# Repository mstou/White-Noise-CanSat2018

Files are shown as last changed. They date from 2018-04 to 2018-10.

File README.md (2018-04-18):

# White Noise
[White Noise](https://www.facebook.com/WhiteNoiseGRE/) is a space-engineering team from the National Technical University of Athens and currently consists of 6 members ( in alphabetical order ) :

 - Dimitris Bralios
 - Chariton Charitonidis
 - Iasonas Nikolaou
 - Spyros Pavlatos
 - George Rapakoulias
 - Miltiadis Stouras

Our team won 1st prize in the [CanSat in Greece 2018](https://cansat.gr/) competition.

# DrillSat
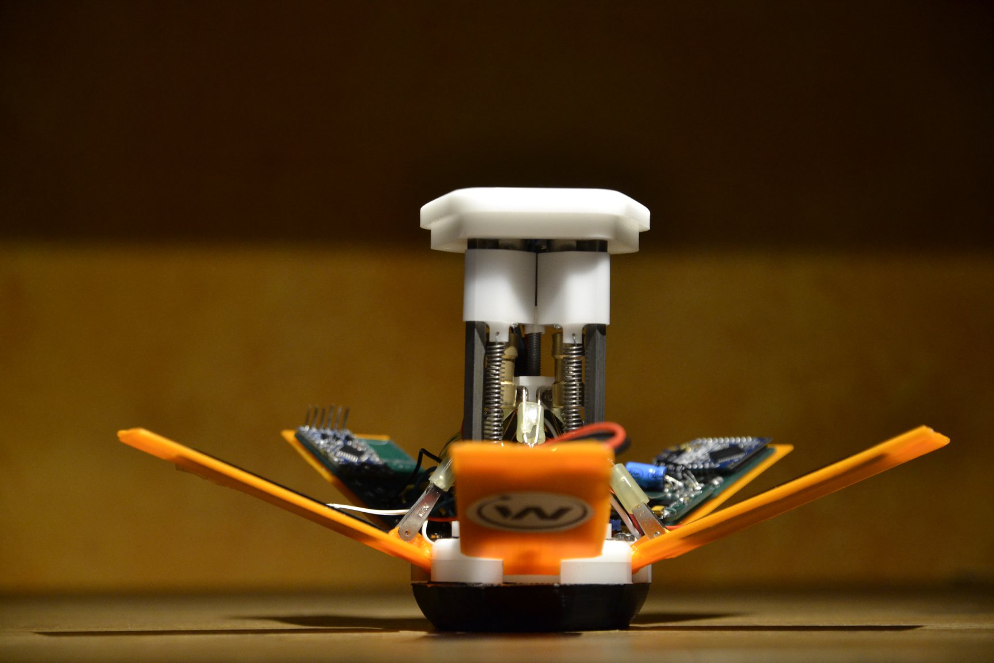
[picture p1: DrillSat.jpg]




This repository hosts the electrical circuits, mechanical drawings and software of our CanSat. Our goal was to develop a CanSat that can help in exploring new planets, as a part of our idea to use CubeSats in space exploration. Specifically, our CanSat, after a successful landing with the parachute, is able to use its [leg mechanism](https://www.youtube.com/watch?v=kTSUgSXn8OM) and rise into a position from which it can dig its drills to the ground and measure the soil's moisture with a sensor we developed.
You can find our ground station [here](https://github.com/MStou/CanSat2018-Ground-Station).

Our team, after facing many difficulties developing the prototype, decided to be fully open source and released all of our work to make sure that future teams will not have to "re-invent the wheel".

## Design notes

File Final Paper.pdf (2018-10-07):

## CFP-18-White-Noise

## CANSAT FINAL PAPER - DRILLSAT

### Authors Dimitris Bralios, bnbzor@gmail.com Chariton Charitonidis, haritoncharitonides@gmail.com Iasonas Nikolaou, iasonasnikolaou11@hotmail.com Spyros Pavlatos, spyrospavlatos4@gmail.com George Rapakoulias, george.rpk@outlook.com Miltiadis Stouras, m.stouras@gmail.com

Abstract: The CanSat in Greece competition aims at giving university students the opportunity to work on a multidisciplinary project with technology similar to that used in small satellites and to take their first steps in space. Moreover, the current trend in satellite technology which is to achieve more with a smaller probe, with prime examples being the CubeSats, makes this kind of competition more relevant. Our goal as a team was to design and build a CanSat that could be the basis for an actual space probe with the aim of extraterrestrial exploration. This paper presents our design of the CanSat discussing the mechanical, electrical and software aspects in detail, while showing that all the mission requirements are met. Specifically, our CanSat is launched onboard a research rocket and deployed at the apogee. Then a parachute is used to reach the nominal descent velocity. Equipped with five legs it is able to reach an upright position from where the drills can be activated. First, the leg and drill mechanisms are described in detail. Next, the selected sensors, the measurements taken and the electronics subsystem are discussed. Then, we present the flight software as well as the ground station that receives and visualizes the mission data in real time. Finally, we discuss the challenges we faced and draw conclusions.

CFP-18-White-Noise | Page 1 of 8

I. INTRODUCTION
The mission of our team for the 2018 CanSat in Greece competition consisted of the primary mission, same for all contestants, and the secondary one, selected by our team. In the primary mission we had to integrate sensors in our design, capable of measuring position, temperature and altitude during descent. The secondary mission was inspired from a number of real life projects in extraterrestrial exploration like the curiosity rover, the rosetta space probe, asteroid mining concepts etc. All those projects revolve around analysing the surface and soil of
planets | or | comets, | encountering | harsh
conditions. Our goal was to build a sensor for estimating soil moisture concentration and monitor it over time, in a supposed target planet, in order to further evaluate whether it could eventually host plants and support human activity. For further analysis, we added a UV sensor, since this is proven to be a key factor in the germination process.

II. PROJECT DESCRIPTION
The CanSat is launched onboard a Patriot type-rocket, with an apogee of 1 km where the probe is deployed. During the flight, a velocity of 500 km/h and an acceleration of 22 g could be reached. Next, throughout the descent the probe measures the barometric pressure, temperature and geographic coordinates. These measurements are stored as well as sent to the ground station in real time.
Requirements include the size of the probe, which has to fit inside a cylinder with a diameter of 65mm and a height of 115 mm. The descent rate after the deployment of the parachute should be in the range of 6 - 10 m/s. Also, the probe should be able to operate 4 hours continuously. Lastly, the mass of the CanSat should not exceed 350 grams.
Goal of the secondary mission is to measure the UV radiation and the soil moisture of the environment the CanSat is deployed in, from which we can exclude crucial information that can help us in our efforts to inhabit the target planet . After a successful landing with the parachute, it is able to use its leg mechanism and rise into a position from which it can dig its drills to the ground and measure the conductivity between the two drills, which is related to the moisture of the soil examined. Apart from the pressure and temperature sensor, a UV light sensor is added to determine if there is spectral content in the UV-A and UV-B range.
The data gathered are sent to the ground station, which is equipped with a high gain Yagi antenna with a range of 3 - 4 km. The frequency of the transmissions is 1 Hz. Through a web application the data received can be displayed and plotted in real time on a computer of the ground station.

III. MECHANICAL SYSTEM
In order to achieve our goals, a number of mechanisms had to be implemented in the design. The small size of the CanSat made it challenging to fit everything inside it in a robust way. After many prototypes, the following layout was chosen.

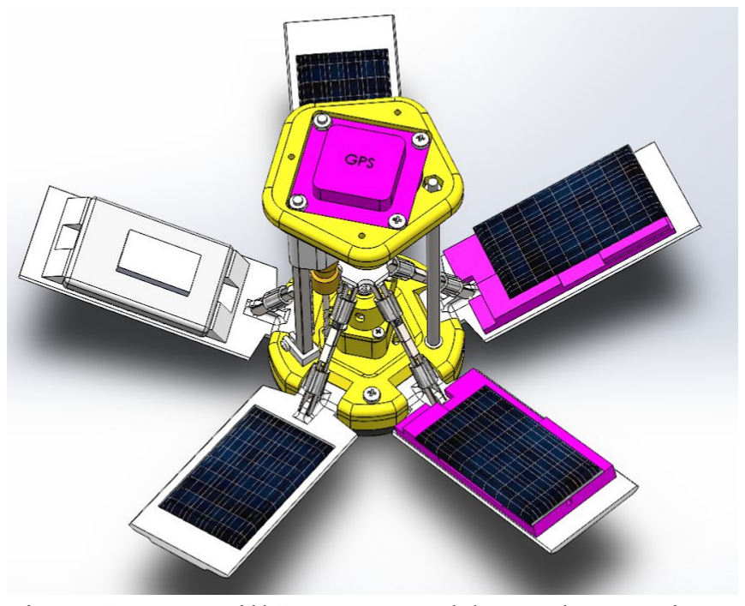
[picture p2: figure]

Fig. 1: DrillSat assembly, electronics represented with purple.

| All the electronics, the battery and the
solar panels were placed on the inside surface of the legs leaving space in the core of the CanSat for the drills and the leg deployment mechanism. A set of 5 foldable legs were placed in the periphery of the satellite, a number chosen to provide a good balance between leg width and near circular top view. A motor driven platform moving on a threaded rod, along with N clevis joints were used for deploying those legs. The length of each arm and the position of the joints were chosen carefully in order to give the mechanism an appropriate mechanical gain, allowing it to operate with a small motor and minimum current.

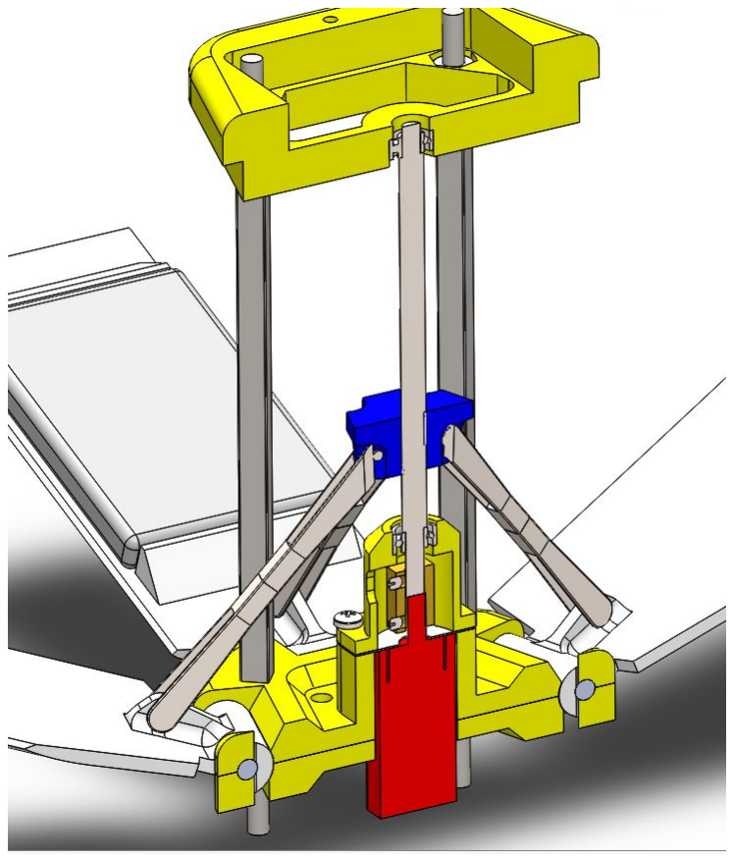
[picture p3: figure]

Fig. 2: Legs deployment mechanism

As for the drill mechanism, the drill assembly was sliding on a square 4x4 mm rod. In order to save space and weight, the assembly was moving with the aid of springs instead of actuators. An expendable retainer was used to prevent the drill from deploying. When voltage was applied to the motors, the drills would penetrate the retainer and protrude out of the CanSat, into the ground.

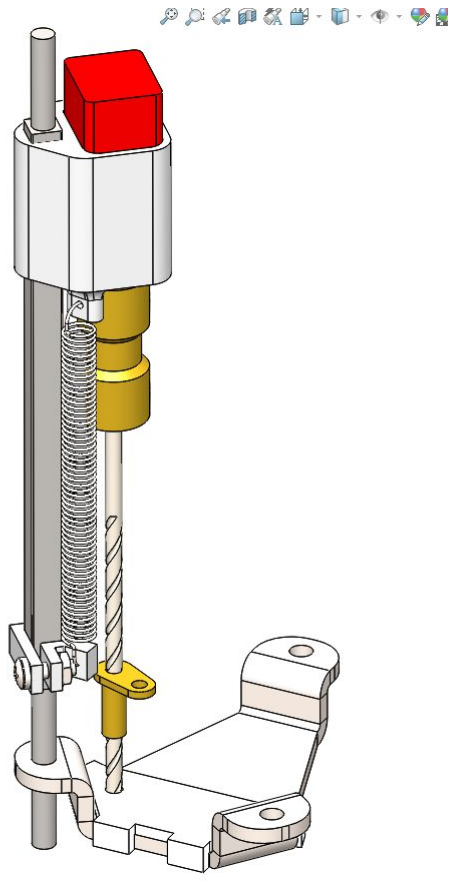
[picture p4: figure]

Fig. 3: Drill mechanism

Finally, in order to provide dampening in hard landings, some extra parts were added. A bottom made from TPC rubber was designed to make the first contact with the ground, absorbing most of the energy from the impact. Because the motor moving the legs was also located in the bottom of the satellite, we added a stainless steel metal cover around it.

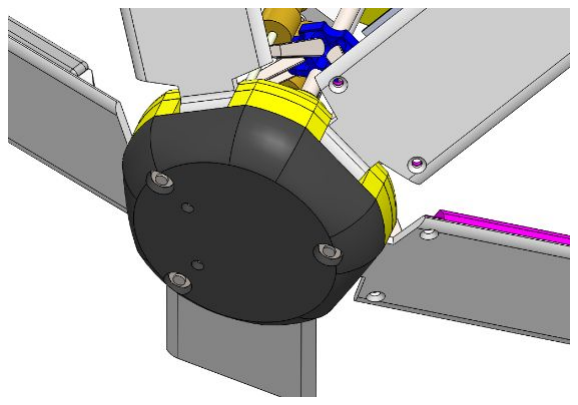
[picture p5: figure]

Fig. 4: Rubber damper

Most parts were CNC machined from POM plastic, ensuring high strength and dimensional precision. Metal parts were all made from stainless steel, with the exception of couplers, which were made from brass.
Apart from the satellite, we also constructed the parachute. We chose a classic circular design with a vent in the apex for stability. Its surface was first calculated theoretically using the following formula
F D = | [1]
2

CD

ρ V A

2

solved for A, given the terminal velocity (V), the total drag force (FD
), the air density (ρ) and the drag coefficient (CD

). After building the first prototype, fine-tuning was made in the surface area in order to achieve our target terminal velocity at 8 m/s, which we measured using image analysis from a video. Later on, for better precision, we also calculated the terminal velocity by conducting several drop tests in which we measured the height of the satellite in small constant time intervals and analyzed the measurements. The material we used was ripstop nylon. The diameter of the parachute was 48 cm and the diameter of the stability vent was 8 cm. A total of 8 buttonholes were made around the perimeter of the parachute fabric. A simple 2 mm kevlar thread was used for the suspension lines whose length was 50 cm enough to minimize the pitch of the CanSat.

IV. ELECTRONICS SYSTEM
The electronics system of the CanSat is comprised of an Arduino microcontroller, a UV sensor, a pressure and temperature sensor, a GPS, an XBee RF module anda conductivity sensor, all powered by a LiPo battery and four solar panels. The system apart from the battery the solar panels and the GPS, has to fit on top of two legs of the CanSat inside a space of 7x35x71 mm. Due to that two PCBs were designed so that the electronics can be mounted onto them. Also the structure had to be robust and survive any stresses, as well as being to run continuously for 4 hours, constricting the power budget.

IV.I. Sensor Subsystem
The UV light sensor used is ML8511 mounted on a board. Equipped with an internal amplifier it converts the photodiode current to voltage, outputting voltage linearly related to the UV light intensity measured in mW/cm

2
. The
sensor output is stable across the operating temperature range, from -25° C up to 75° C, although, when measuring in temperatures away from the one on which the sensor was calibrated, a slight error is introduced. The spectral response is highest in the range 280 - 390 nm which covers the UV-B spectrum and significant percentage of the UV-A spectrum. The typical supply current is around 300 μA at the operational voltage of 3 V.

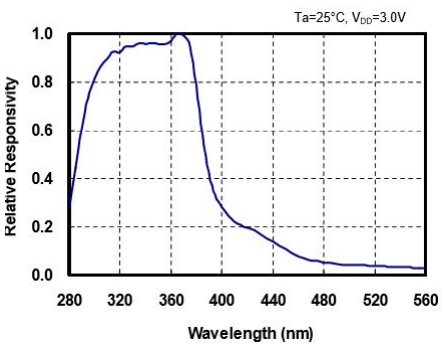
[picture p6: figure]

Fig. 5: Spectral response characteristics of ML8511

| The sensor used to measure temperature
and barometric pressure is BMP280. The interface used to communicate with the microcontroller is I2C. The pressure and temperature data, using the barometric formula, can give the current height with an accuracy of 1m. The operating pressure range is up to 9000 m above sea level and from -40° C to 85° C regarding the temperature range, while the typical current drawn is 2.7 μA.
The sensor used to measure the soil moisture is implemented as a voltage divider. Two high speed steel drills spaced 18.2mm apart are used to penetrate 20 mm in depth. One drill is connected to the ground voltage level through a 10K Ohm resistor while the other one to the +3.3 V level. The former drill is connected to an analog pin of the microcontroller. Given the voltage at that pin we can specify the resistance between them and then calculate the soil moisture.
The GPS module used is the LEA-6H, which is mounted on the top of the CanSat. It
sends | NAV-POSLLH | packages | to | the
microcontroller via serial connection, at a frequency of 1Hz. Typical supply current is 41 mA and 47 mA during the acquisition phase and the horizontal accuracy is 2.5 m.

IV.II. Communication and Data Handling The selected microcontroller board is the Arduino Pro Mini, using the ATmega328P, an 8-bit AVR microprocessor. It runs at 3.3 V and 8 MHz and has 14 input/output pins, 6 of them analog. The available program memory size is 32 KByte, as well as 1024 Bytes of non volatile EEPROM memory, used to make the CanSat state-aware after possible power offs. Apart from collecting and processing the measurements of the sensors the Arduino also controls the three motors through N-channel MOSFETS.
The RF module used for communication with the ground station is the XBee Pro S5 operating at 868MHz. It runs on 3.3 V consuming 60 mA at stand-by mode, 200 mA on packet emission and has a sensitivity of -112 dBm. It is used with an external antenna with 3 dBi gain which has the following radiation pattern.

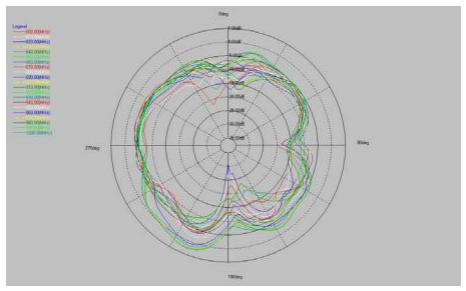
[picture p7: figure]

Fig. 6: Radiation pattern of the probe’s antenna

The same XBee module is also used on the ground station. The two modules are programmed to operate on AT Mode with ground station’s XBee being the coordinator and cansat’s XBee a router. Both modules transmit at a power of 25mW which is the legal local limit at 868MHz.

IV.III. Electrical Power Subsystem
A Polymer Lithium Ion battery, charged by four solar panels, is powering the CanSat. The battery has a voltage output of 3.7 V and a capacity of 980 mAh. Four 30.5 mm by 58.5 mm solar panels connected serially are used to charge the battery through the MCP73871. Then a low-dropout regulator drops the voltage down to 3.3 V powering every piece of electronics, except for the GPS, which has an onboard regulator, and the three motors.

Voltage
(V)

Current
(mA)

Power
(mW)
Arduino | 3.3 | 25 | 82.5
XBee | 3.3 | 60 | 198
GPS | 3.7 | 50 | 165
SD card | 3.3 | 30 | 99
BMP sensor 3.3 | 1 | 3.3
UV sensor | 3.3 | 0.5 | 1.65
Motors | 3.7 | 350 | 1295
Table 1: Power budget
Through experiments the previous values of current drawn were found. We conclude that the battery selected is able to power the CanSat for the required time duration.
V. FLIGHT SOFTWARE
The flight software consists of three software states: Launching, Descent and Ground Operations. In each state, the sequence of events is:
1. Take measurements
2. Save measurements to SD Card
3. Send a telemetry package containing the last measurements to ground station
4. Process data and determine the new software state

To ensure that our mission’s state is maintained through unexpected processor resets, some information regarding the current state is stored on the non-volatile memory (EEPROM) of the microcontroller, so it can be queried on processor start-up. Being able to dynamically determine our software state is vital for the success of the flight software because a simple sequential program could get stuck in the wrong software state after a sudden reset and lose control of the mission. The flight software is visualised in the flowchart of Fig. 7.

VI. GROUND CONTROL SYSTEM
The ground station consists of a personal computer, an Xbee Pro S5 and a Yagi Antenna with 8 dBi gain. The Xbee is connected via USB to the computer, and the Yagi Antenna is attached to the Xbee module with an RP-SMA connector. The data received by the computer, is parsed by a python script, checked for errors, and saved in a JSON format. Meanwhile a node.js server running locally serves a web page where the data is plotted in real-time using React.js and plotly.js.

VII. CONCLUSION
If we were to rebuild the satellite, we would have made a number of changes, both in the mechanisms and the circuits. One thing we found particularly hard was integrating all cables in the design. Lack of space along with the fact that the circuit boards were in moving parts of the cansat made this even harder. Using cable ribbons and socket connectors would give better results as well. Furthermore, a future upgrade would be the design of PCBs that host most of the electronics components, the sensors themselves and not serving as connectors between various sensor boards. Lastly, another minor enhancement would be to establish a 2-way communication with the satellite, changing the antennas’ and the software accordingly, in order to be able to query the satellite for values that are typically not included in mission’s telemetry packages (i.e. values stored in EEPROM), as well as have it to execute orders given from the ground station in real-time.
In conclusion, with the end of this project, our team has gained significant knowledge and experience. We believe that by constructing DrillSat we have proved our initial standing, that CanSats and CubeSats can include complex mechanisms and be used in a wide variety of space missions (such as extraterrestrial exploration) .

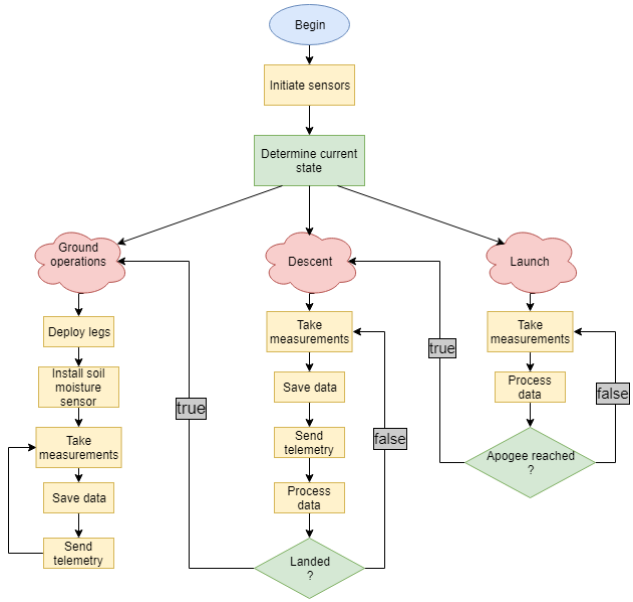
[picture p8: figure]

Fig. 7: Flight software flowchart

VII. REFERENCES
-CanSat in Greece portal: www.cansat.gr -Christos Papadopoulos, Machine Design, 3rd edition 2017
-UV Sensor with Voltage Output. ML8511. Rev. 5.0. Lapis Semiconductor. Mar. 2013.
-Digital Pressure Sensor. BMP280. Rev. 1.14. Bosch Sensortec. Mar. 2015.
-LEA-6 u-blox 6 GPS Modules. UBX-14044797. Rev. 13.0. U-blox. Feb. 2017.
-8-bit | AVR | Microcontrollers.
Atmel-42735B-ATmega328/P. Rev. B. Atmel. Nov. 2016.
-XBee-PRO 868 RF Module. Rev. F. Digi International. May. 2015.
-Polymer Lithium-Ion Battery. LP573450. Rev. 1.0. Cellevia Batteries. May. 2017.
-Stand-Alone | System | Load | Sharing | and
Li-Ion/Li-Polymer Battery Charge Management Controller. MCP73871. Rev. C. Microchip Technology. Sep. 2013.
-Arduino Documentation: www.arduino.cc

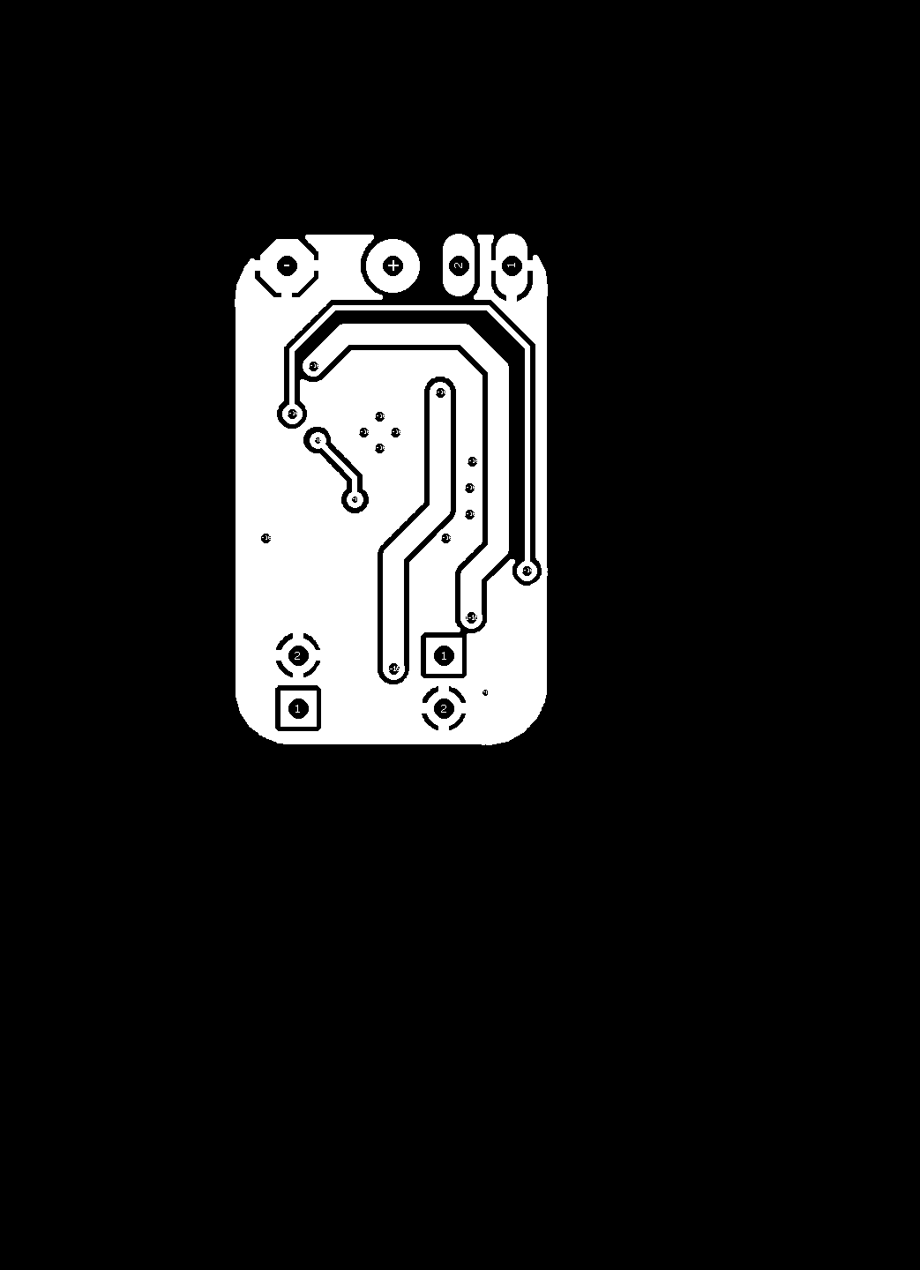
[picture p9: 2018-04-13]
Circuits/Charger/NEW.sol.bmp

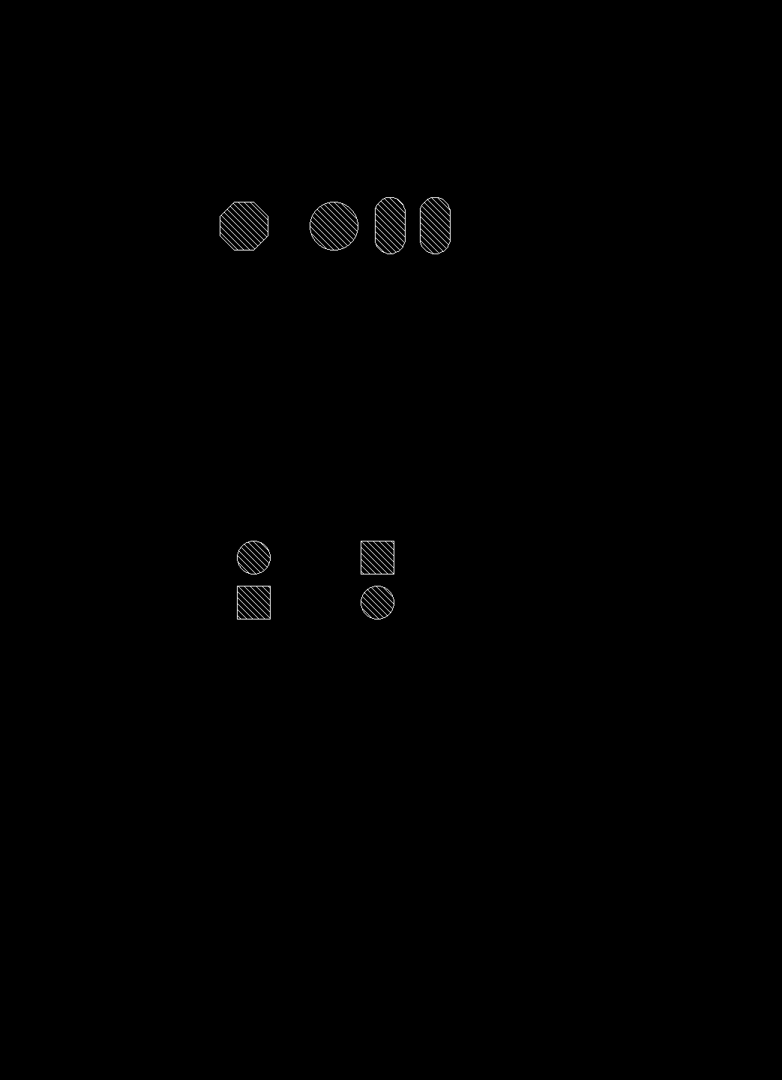
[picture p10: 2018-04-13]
Circuits/Charger/NEW.sts.bmp

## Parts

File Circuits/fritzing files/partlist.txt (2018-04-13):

Partlist

Exported from NEW.brd at 14/3/2018 11:14 ìì

EAGLE Version 8.5.0 Copyright (c) 1988-2017 Autodesk, Inc.

Assembly variant: 

Part     Value          Package    Library      Position (mm)         Orientation

C1       10uF           C0805K     adafruit     (13.588 3.54)         R270		// http://gr.rsdelivers.com/product/kemet/c0805c106k9pactu/kemet-10%CE%BCf-multilayer-ceramic-capacitor-mlcc-63v/4516290
C2       10uF           C0805K     adafruit     (5.715 2.874)         R90
C3       10uF           C0805K     adafruit     (1.192 13.366)        R270
D1       MBR120VLSFT1G  SOD-123    microbuilder (11.556 19.971)       R0 		// http://gr.rsdelivers.com/product/on-semiconductor/mbr120vlsft1g/on-semi-mbr120vlsft1g-smt-schottky-diode-20v-1a-2/7815626
IC1      MCP73871       QFN20_4MM  adafruit     (6.907 14.986)        R0		// http://gr.rsdelivers.com/product/microchip/mcp73871-2cci-ml/microchip-mcp73871-2cci-ml-lithium-ion-lithium/6696199
R2       270K           R0805      adafruit     (7.478 7.572)         R90
R3       100K           R0805      adafruit     (11.177 8.334)        R180		// http://gr.rsdelivers.com/product/bourns/cr0805-fx-1003elf/bourns-cr0805-series-thick-film-fixed-resistor/7883997P
R5       1K             M0805      adafruit     (3.652 11.43)         R270
R11      2K             M0805      adafruit     (13.13 17.272)        R270
R12      100K           R0805      adafruit     (13.384 12.652)       R90		// http://gr.rsdelivers.com/product/bourns/cr0805-fx-1003elf/bourns-cr0805-series-thick-film-fixed-resistor/7883997P
RT2      150K           M0805      adafruit     (2.652 7.256)         R90
THERM    10K            M0805      adafruit     (5.112 6.986)         R90

3.3V Regulator
4 N channel MOSFET

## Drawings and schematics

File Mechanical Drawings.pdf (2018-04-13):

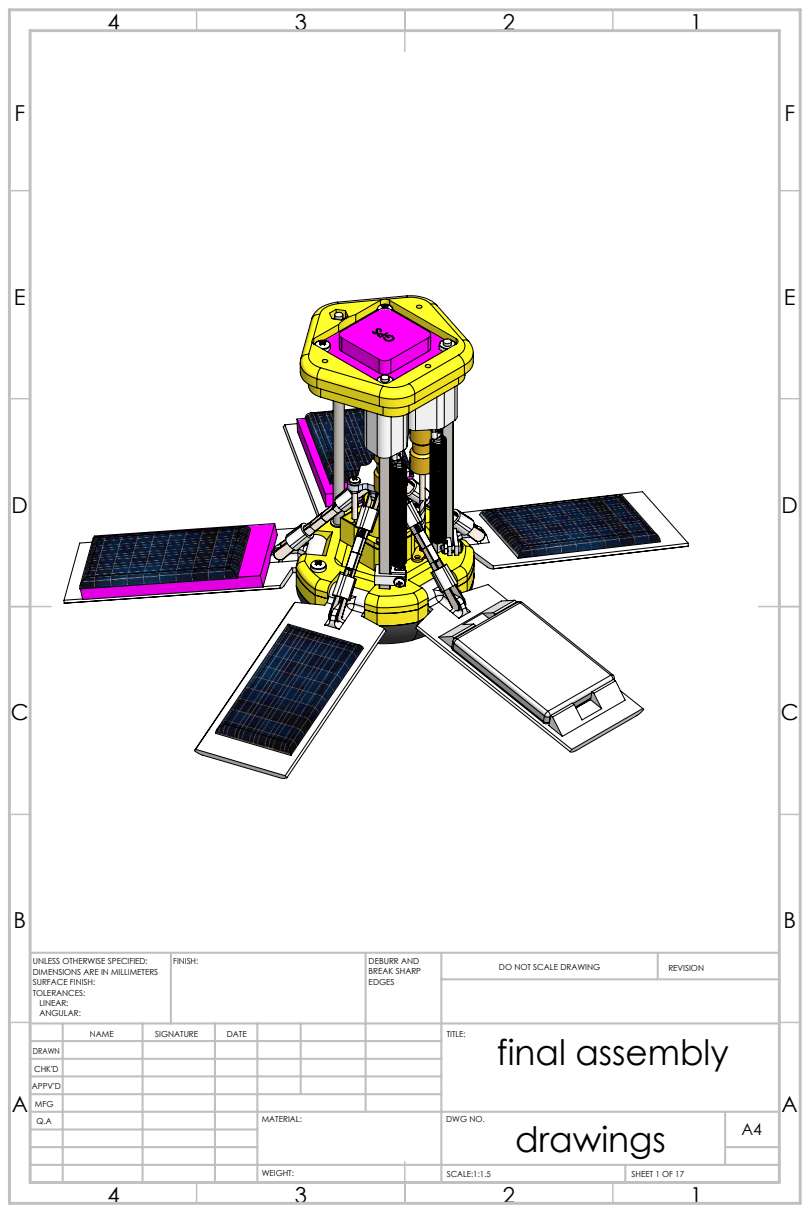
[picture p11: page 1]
FINISH:; DEBURR AND; BREAK SHARP; DO NOT SCALE DRAWING; REVISION; SCALE:1:1.5; SHEET 1 OF 17

UNLESS OTHERWISE SPECIFIED:
DIMENSIONS ARE IN MILLIMETERS
SURFACE FINISH:
TOLERANCES:
LINEAR:
ANGULAR:

NAME | SIGNATURE | DATE | | | | TITLE: final assembly

DRAWN
CHK'D
APPV'D
MFG
Q.A | | | | MATERIAL: | DWG NO. drawings | A4

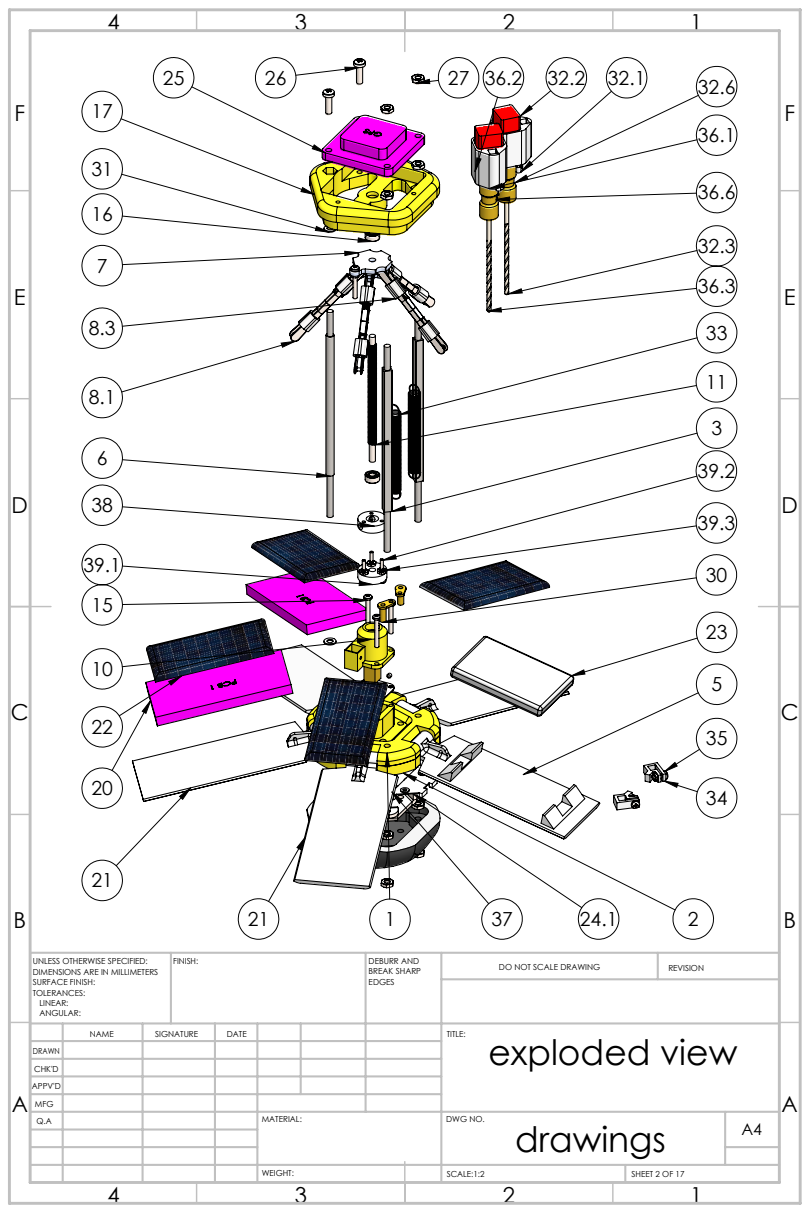
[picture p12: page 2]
FINISH:; DEBURR AND; BREAK SHARP; DO NOT SCALE DRAWING; REVISION; SCALE:1:2; SHEET 2 OF 17

UNLESS OTHERWISE SPECIFIED:
DIMENSIONS ARE IN MILLIMETERS
SURFACE FINISH:
TOLERANCES:
LINEAR:
ANGULAR:

NAME | SIGNATURE | DATE | TITLE: exploded view

DRAWN
CHK'D
APPV'D
MFG

ITEM NO. | PART NUMBER | MATERIAL | QTY.
1 | level 0 | cnc POM | 1
2 | level 0 | cnc POM | 1
3 | frame shaft | stainless steel | 2
4 | leg shaft | stainless steel | 5
5 | leg | ABS 3d printed | 1
6 | frame shaft | stainless steel | 1
7 | cable joint | cnc POM | 1
8 | leg arm | | 5
8.1 | N clevis | | 2
8.2 | clevis connecting bolt | standard M2 strud bolt | 1
8.3 | safety tube | silicon tube | 2
9 | motor plate | laser cut steel sheet | 1
10 | motor bearing bracket | cnc POM | 1
11 | power bolt | stainless steel | 1
12 | motor | 45 RPM 6V geared motor | 1
13 | coupler | brass | 1
14 | socket set screw cup point_am | | 2
15 | ISO 7045 - M2 x 16 - Z -16N | | 3
16 | AFBMA 20.1 - 38-3 -10,DE,NC,10_68 | | 2
17 | level 1 | cnc POM | 1
18 | DIN EN ISO 7045 - M2 x 16 - Z - 16N | | 1
19 | Hexagon Thin Nut ISO 4035 - M2 - N | | 3
20 | pcb 1 | | 2
21 | leg | ABS 3d printed | 4
22 | solar cell | | 4
A | A
B | | B
| NAME | SIGNATURE | DATE | TITLE: bill of materials
DRAWN
CHK'D
APPV'D
MFG
C | C
D | D
E | E
F | F

UNLESS OTHERWISE SPECIFIED: DIMENSIONS ARE IN MILLIMETERS SURFACE FINISH:
TOLERANCES:
LINEAR:
ANGULAR:
FINISH: | DEBURR AND
BREAK SHARP
EDGES
DO NOT SCALE DRAWING | REVISION
SCALE:1:1 | SHEET 3 OF 17

ITEM NO. | PART NUMBER | MATERIAL | QTY.
23 | battery 960 mAh | LiPo | 1
24 | shield | laser cut steel sheet | 1
24.1 | | Sheet | -
25 | GPS | | 1
26 | pan head cross recess screw_din | | 2
27 | Hexagon Thin Nut ISO 4035 - M3 - N | | 13
28 | DIN EN ISO 7045 - M3 x 16 - Z - 16N | | 2
29 | damper | molded rubber | 1
30 | drill contact | brass | 2
31 | DIN 988-3x6x0.5 | | 2
| 32 | drill right | | 1
| 32.1 | drill motor holder | | 1
| 32.2 | motor | 450 RPM 6V geared motor | 1
| 32.3 | drill bit | HSS steel | 1
| 32.4 | DIN 914 - M2 x 3-N | | 2
| 32.5 | DIN EN ISO 7045 -M1.6 x 3 - Z - 3N | | 2
| 32.6 | 2-3mm coupler | brass | 1
| 33 | extension spring | stainless steel custom made | 2
| 34 | spring holder | 3d printed | 2
| 35 | pan head cross recess screw_din | | 2
| 36 | drill left | | 1
| 36.1 | drill motor holder | cnc POM | 1
| 36.2 | motor | 450 RPM 6V geared motor | 1
B | 36.3 | drill bit | HSS steel | 1 | B
| 36.4 | DIN 914 - M2 x 3-N | | 2
| 36.5 | DIN EN ISO 7045 -M1.6 x 3 - Z - 3N | | 2
A | A
C | C
D | D
E | E
F | F

UNLESS OTHERWISE SPECIFIED: DIMENSIONS ARE IN MILLIMETERS SURFACE FINISH:
TOLERANCES:
LINEAR:
ANGULAR:
FINISH: | DEBURR AND BREAK SHARP EDGES
| NAME | SIGNATURE | DATE | TITLE: bill of materials
DRAWN
CHK'D
APPV'D
MFG
DO NOT SCALE DRAWING | REVISION
SCALE:1:2 | SHEET 4 OF 17

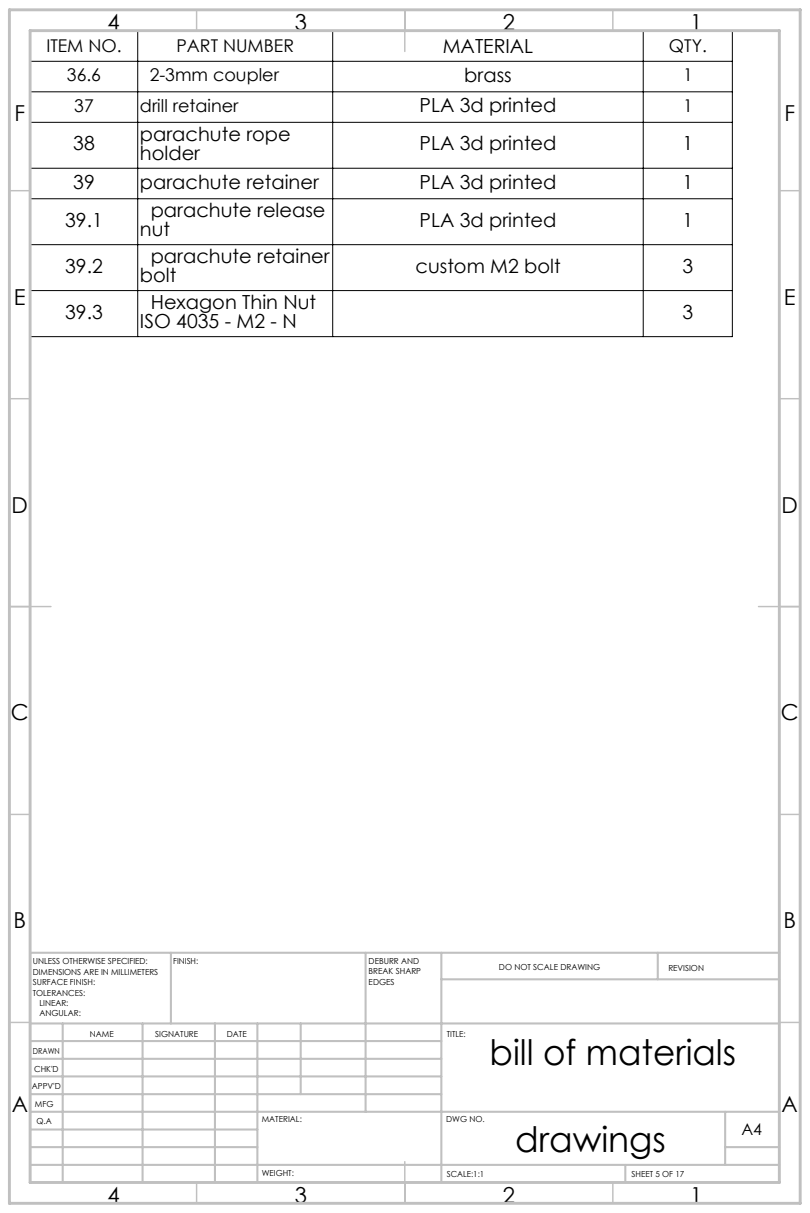
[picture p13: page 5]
ITEM NO.; PART NUMBER; MATERIAL; QTY.; FINISH:; DEBURR AND; BREAK SHARP; DO NOT SCALE DRAWING; REVISION

36.6 | 2-3mm coupler | brass | 1
37 | drill retainer | PLA 3d printed | 1
38 | parachute rope holder | PLA 3d printed | 1
39 | parachute retainer | PLA 3d printed | 1
39.1 | parachute release nut | PLA 3d printed | 1
39.2 | parachute retainer bolt | custom M2 bolt | 3
39.3 | Hexagon Thin Nut ISO 4035 - M2 - N | | 3

UNLESS OTHERWISE SPECIFIED:
DIMENSIONS ARE IN MILLIMETERS
SURFACE FINISH:
TOLERANCES:
LINEAR:
ANGULAR:

NAME | SIGNATURE | DATE | TITLE: bill of materials

DRAWN
CHK'D
APPV'D
MFG

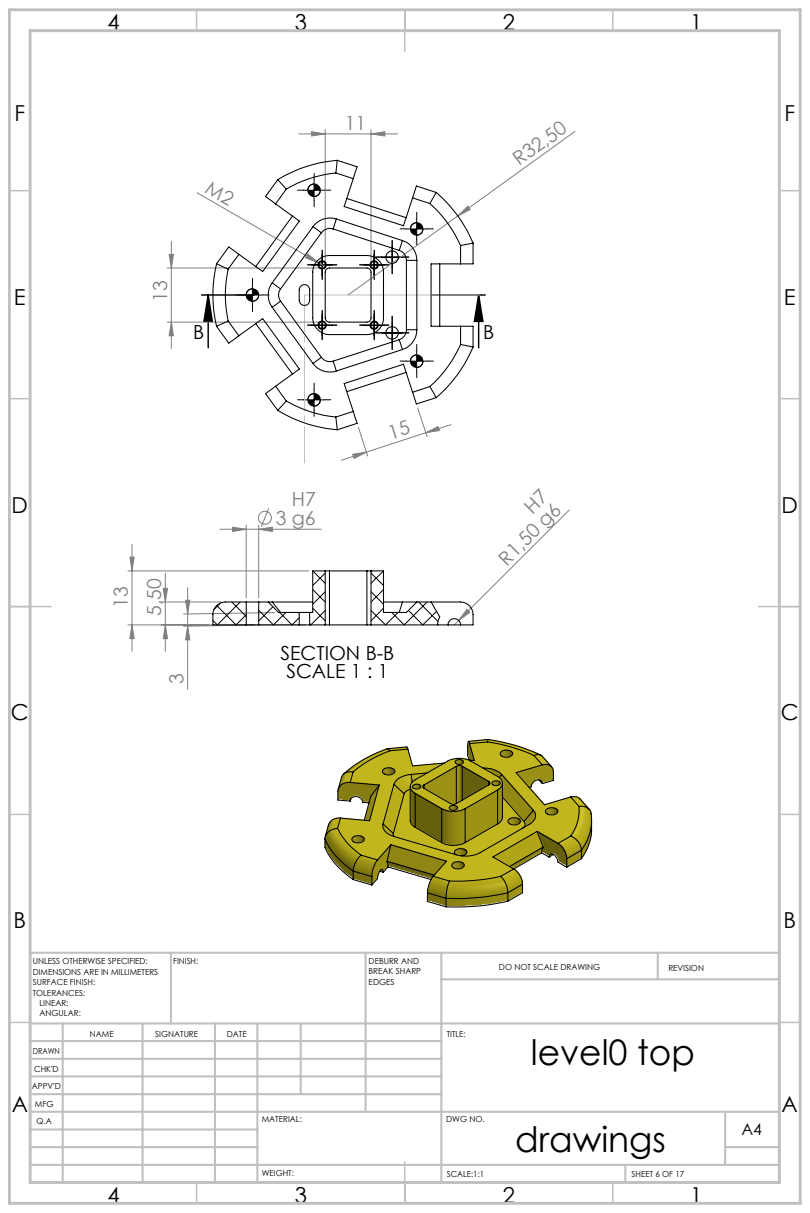
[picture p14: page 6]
SECTION B-B SCALE 1 : 1; FINISH:; DEBURR AND; BREAK SHARP; DO NOT SCALE DRAWING; REVISION

UNLESS OTHERWISE SPECIFIED:
DIMENSIONS ARE IN MILLIMETERS
SURFACE FINISH:
TOLERANCES:
LINEAR:
ANGULAR:

NAME | SIGNATURE | DATE | TITLE: level0 top

DRAWN
CHK'D
APPV'D
MFG

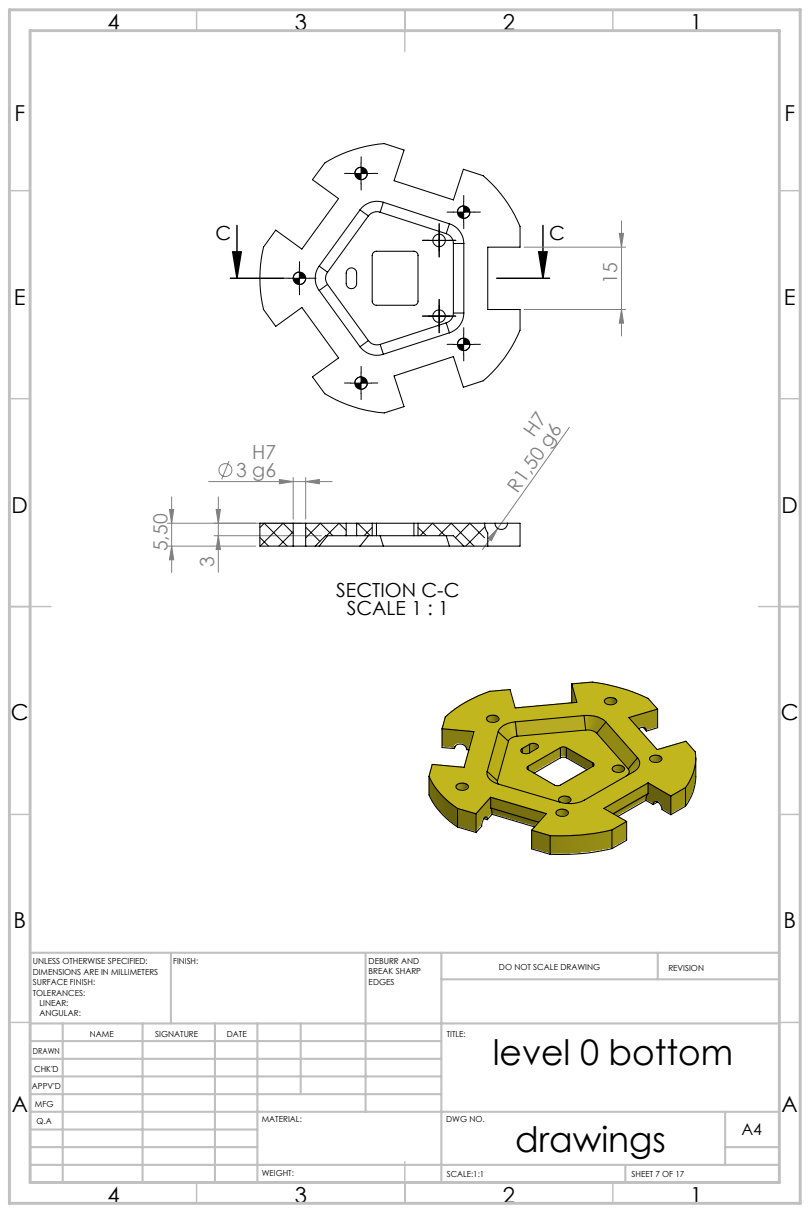
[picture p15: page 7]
SECTION C-C SCALE 1 : 1; FINISH:; DEBURR AND; BREAK SHARP; DO NOT SCALE DRAWING; REVISION

UNLESS OTHERWISE SPECIFIED:
DIMENSIONS ARE IN MILLIMETERS
SURFACE FINISH:
TOLERANCES:
LINEAR:
ANGULAR:

NAME | SIGNATURE | DATE | TITLE: level 0 bottom

DRAWN
CHK'D
APPV'D
MFG

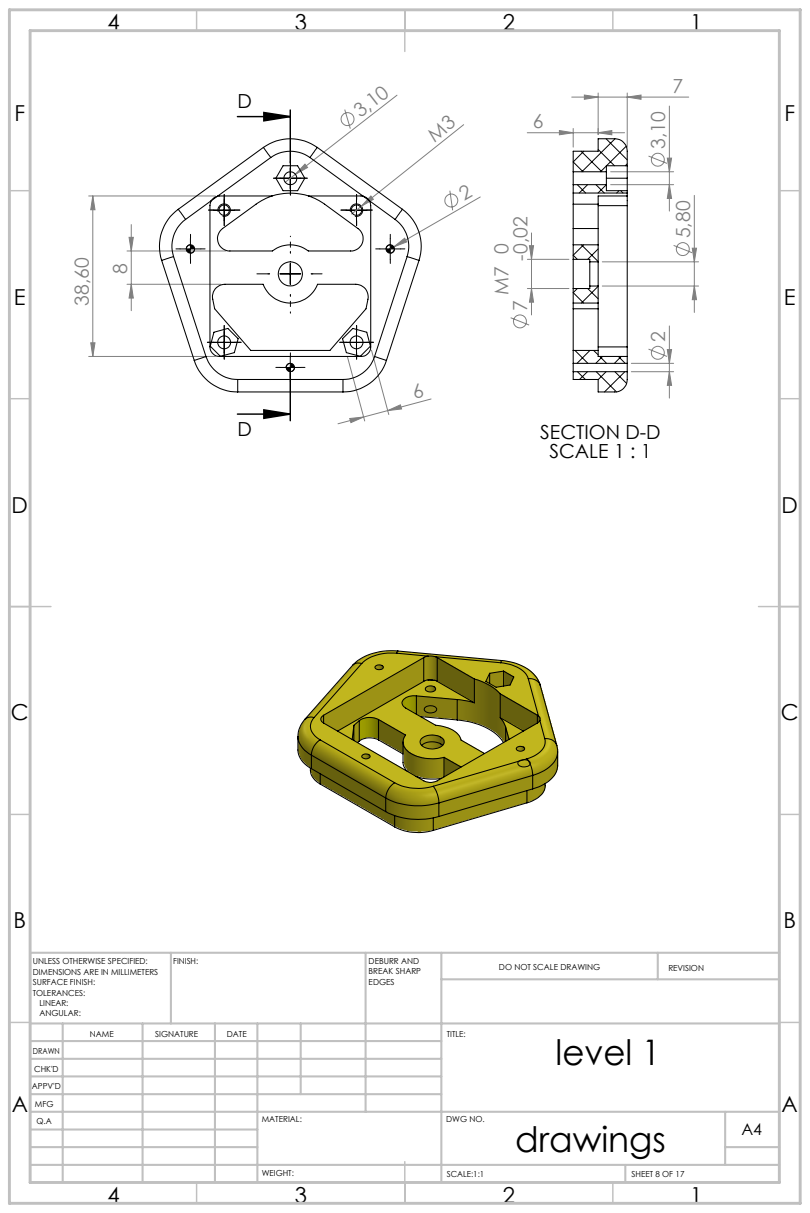
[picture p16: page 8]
SECTION D-D SCALE 1 : 1; FINISH:; DEBURR AND; BREAK SHARP; DO NOT SCALE DRAWING; REVISION
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

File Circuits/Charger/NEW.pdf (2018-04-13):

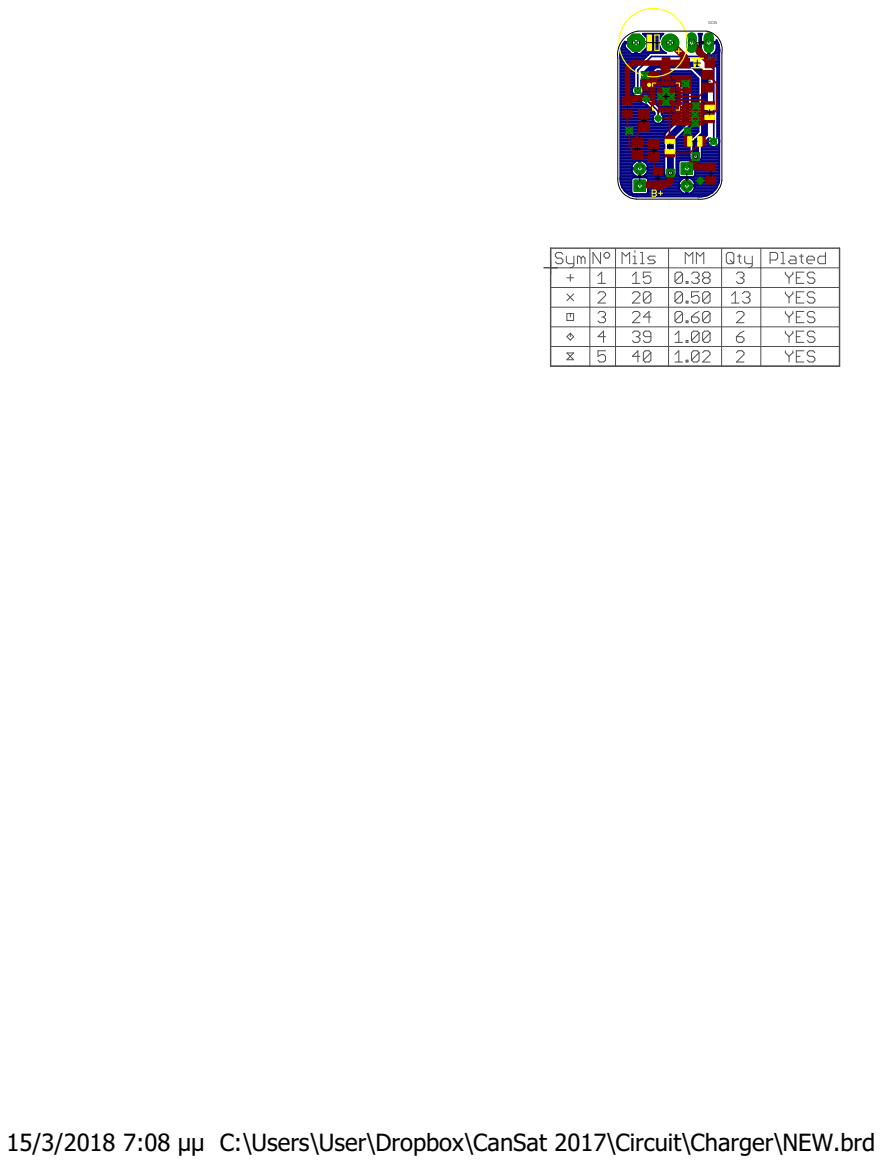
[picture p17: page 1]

15/3/2018 7:08 μμ C:\Users\User\Dropbox\CanSat 2017\Circuit\Charger\NEW.brd

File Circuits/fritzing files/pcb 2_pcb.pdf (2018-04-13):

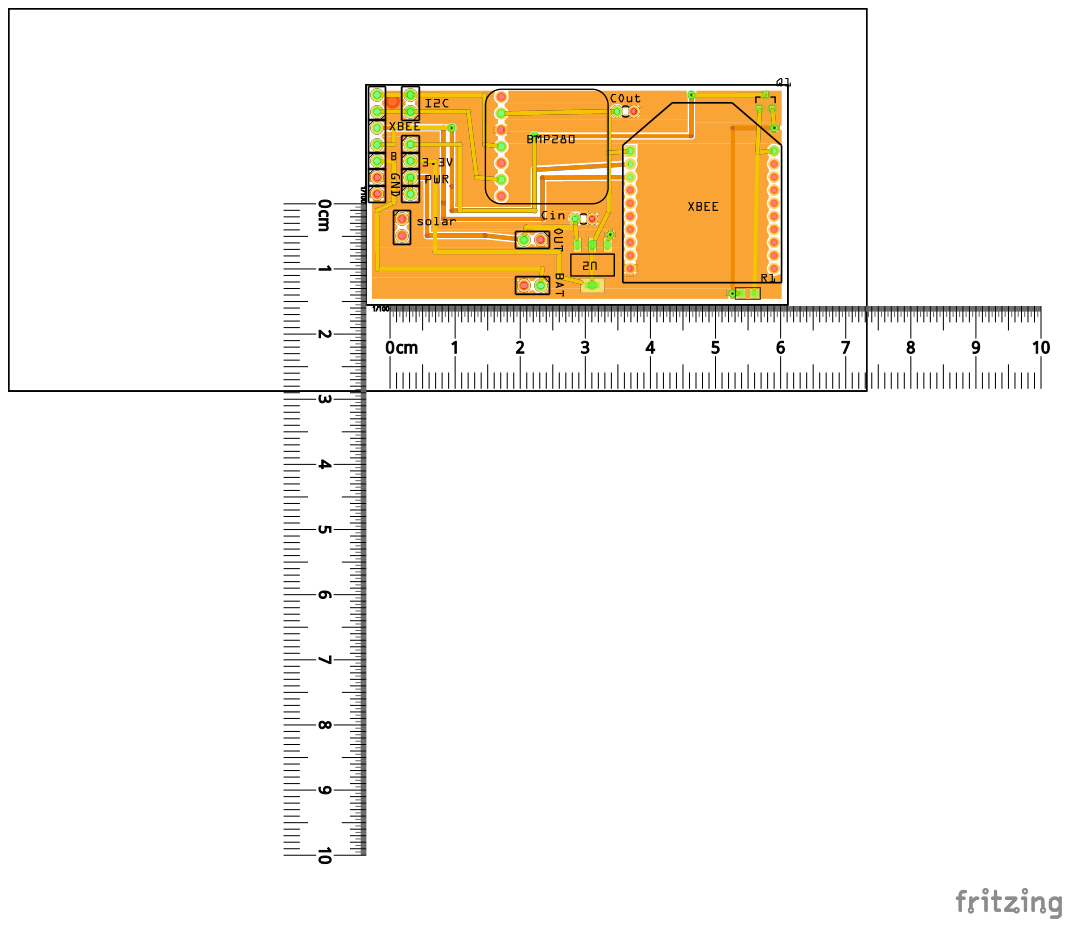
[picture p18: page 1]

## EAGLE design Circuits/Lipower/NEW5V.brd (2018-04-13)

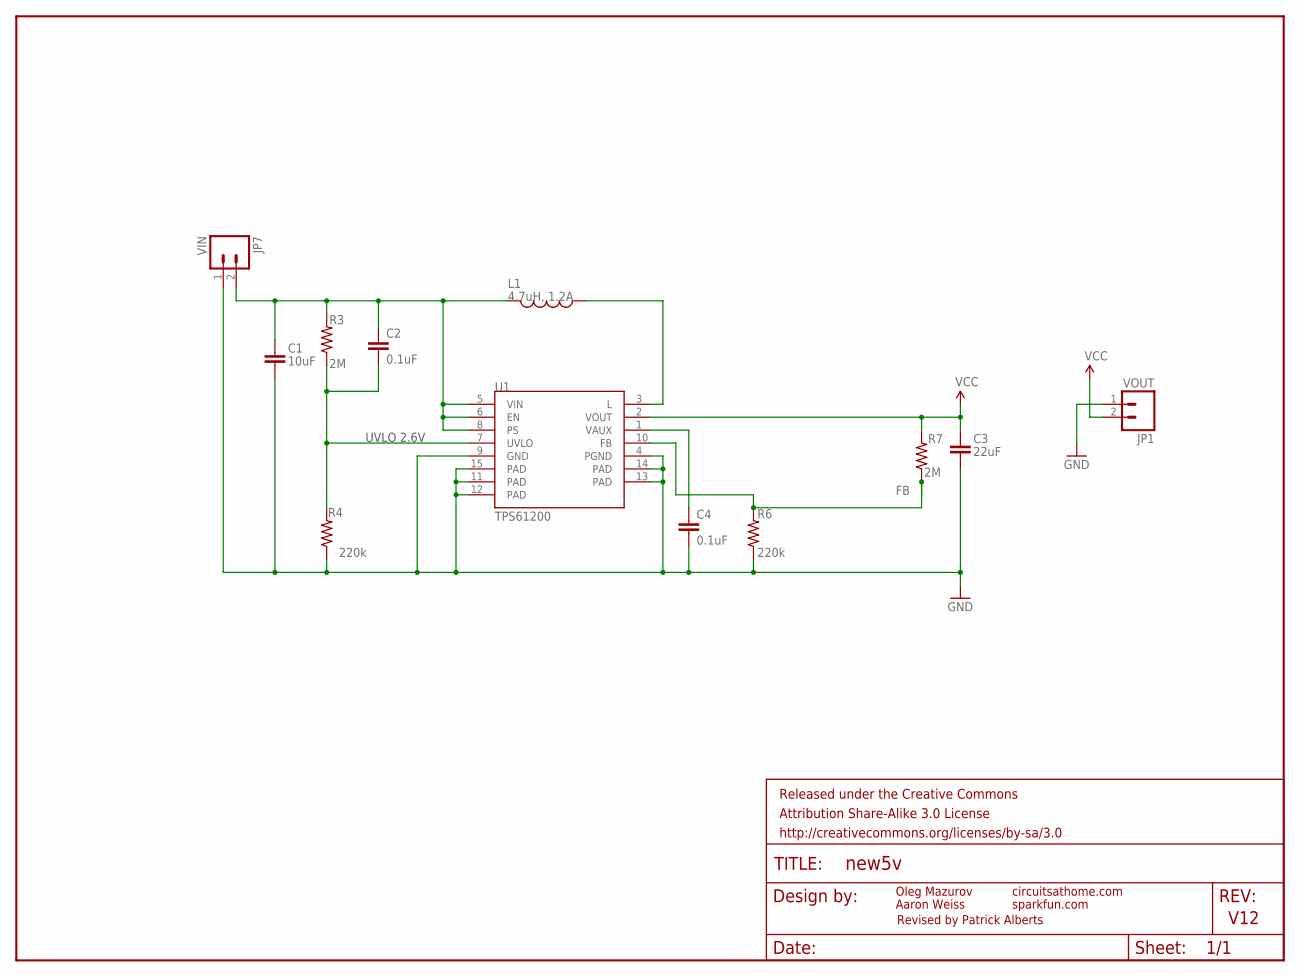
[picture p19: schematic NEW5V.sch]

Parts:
C1: 10uF; 1206
C2, C4: 0.1uF; 0603-CAP
C3: 22uF; 0805
FRAME1: FRAME-LETTER; CREATIVE_COMMONS
JP1: VOUT; 1X02
JP7: VIN; 1X02
L1: 4.7uH, 1.2A; CDRH2D09
R3, R7: 2M; 0603-RES
R4, R6: 220k; 0603-RES
U1: TPS61200; QFN-10_PAD

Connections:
FB: R6.2, R7.1, U1.10 (FB)
GND: C1.2, C3.2, C4.2, JP1.1, JP7.1, R4.1, R6.1, U1.4 (PGND), U1.9 (GND), U1.11 (PAD), U1.12 (PAD), U1.13 (PAD), U1.14 (PAD), U1.15 (PAD)
unnamed: C4.1, U1.1 (VAUX)
unnamed: L1.P$1 (1), U1.3 (L)
UVLO: C2.2, R3.1, R4.2, U1.7 (UVLO)
VCC: C3.1, JP1.2, R7.2, U1.2 (VOUT)
VIN: C1.1, C2.1, JP7.2, L1.P$2 (2), R3.2, U1.5 (VIN), U1.6 (EN), U1.8 (PS)

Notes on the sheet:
UVLO 2.6V
circuitsathome.com
Oleg Mazurov
Aaron Weiss
sparkfun.com
V12
Revised by Patrick Alberts

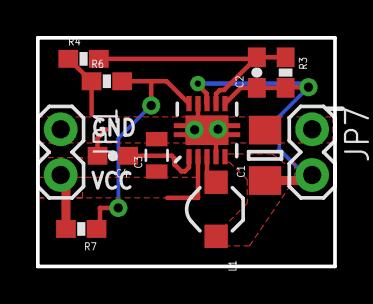
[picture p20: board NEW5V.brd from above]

Board: 2 copper layers, 16.5 x 12.7 mm, 13 parts (0 on the bottom side), 7 nets.

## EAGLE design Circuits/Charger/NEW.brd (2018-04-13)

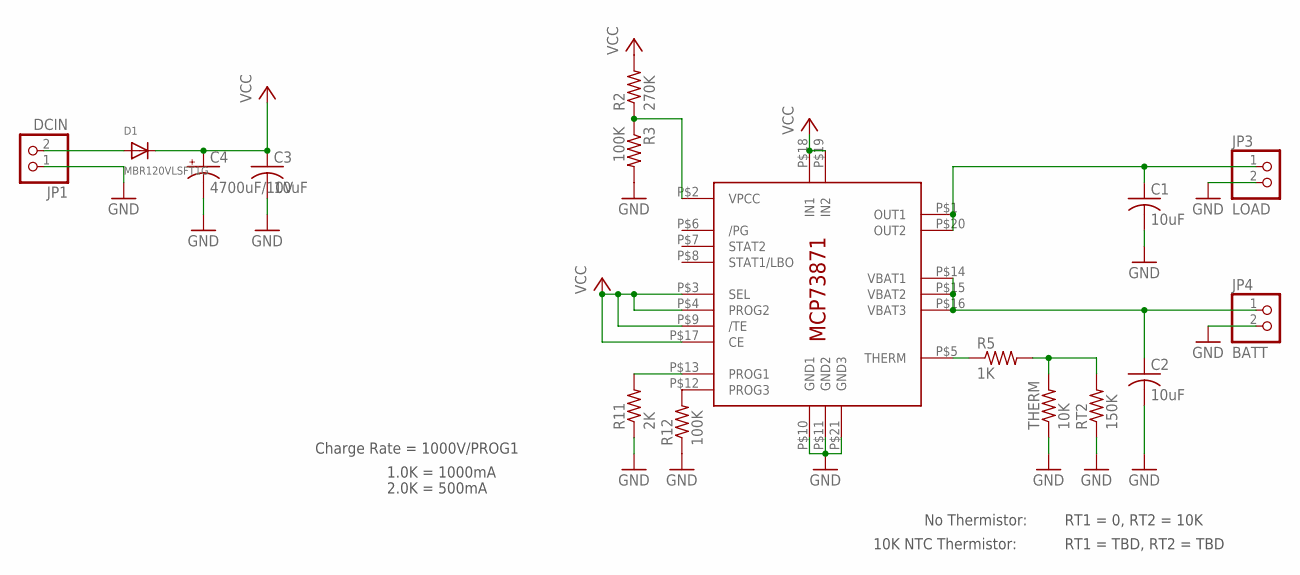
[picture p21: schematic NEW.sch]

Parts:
C1, C2, C3: 10uF; C0805K
C4: 4700uF/10V; E5-10,5
D1: MBR120VLSFT1G; SOD-123
IC1: MCP73871; QFN20_4MM
JP1: DCIN; 1X02_OVAL
JP3: LOAD; 1X02_ROUND
JP4: BATT; 1X02_ROUND
R2: 270K; R0805
R3, R12: 100K; R0805
R5: 1K; M0805
R11: 2K; M0805
RT2: 150K; M0805
THERM: 10K; M0805

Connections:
BATT: C2.1, IC1.P$14 (VBAT1), IC1.P$15 (VBAT2), IC1.P$16 (VBAT3), JP4.1
GND: C1.2, C2.2, C3.2, C4.-, IC1.P$10 (GND1), IC1.P$11 (GND2), IC1.P$21 (GND3), JP1.1, JP3.2, JP4.2, R3.2, R11.1, R12.1, RT2.1, THERM.1
unnamed: D1.A, JP1.2
unnamed: IC1.P$5 (THERM), R5.1
unnamed: IC1.P$2 (VPCC), R2.1, R3.1
unnamed: R5.2, RT2.2, THERM.2
unnamed: IC1.P$12 (PROG3), R12.2
unnamed: IC1.P$13 (PROG1), R11.2
OUT: C1.1, IC1.P$1 (OUT1), IC1.P$20 (OUT2), JP3.1
VCC: C3.1, C4.+, D1.C, IC1.P$3 (SEL), IC1.P$4 (PROG2), IC1.P$9 (/TE), IC1.P$17 (CE), IC1.P$18 (IN1), IC1.P$19 (IN2), R2.2

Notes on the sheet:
Charge Rate = 1000V/PROG1
1.0K = 1000mA
2.0K = 500mA
No Thermistor:
10K NTC Thermistor:
RT1 = 0, RT2 = 10K
RT1 = TBD, RT2 = TBD

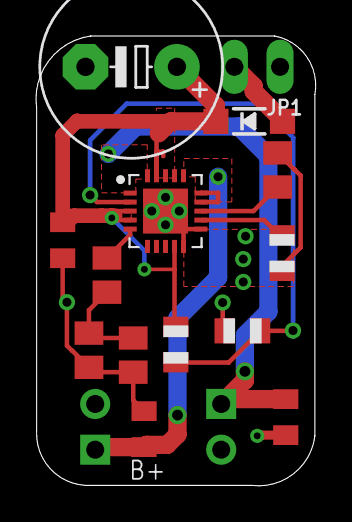
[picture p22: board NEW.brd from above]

Board: 2 copper layers, 15.5 x 25.0 mm, 16 parts (0 on the bottom side), 10 nets.

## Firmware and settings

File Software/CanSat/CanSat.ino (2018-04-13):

#include <Wire.h>
#include <SPI.h>
#include <SD.h>
#include <SoftwareSerial.h>
#include <Adafruit_Sensor.h>
#include <Adafruit_BMP280.h>
#include <EEPROM.h>

#define GPSRxPin 4 //gps' tx connected to GPSRxpin
#define GPSTxPin 3 //gps' rx
#define XbeeTxPin 7 // xbee's tx
#define XbeeRxPin 8 // xbee's rx 
#define SD_Pin 10

#define LegMotor 6
#define DrillMotor1 5
#define DrillMotor2 9
#define LegsButton 2

#define BMP_HEIGHT 350 // these are heights from sea level
#define GPS_HEIGHT 350 // the height at the location of the launch was 170m


struct telemetry_data1{
  double longtitude;
  double latitude;
  double height;
  double pressure;
  double temperature;
  double check_sum;
};

struct telemetry_data2{
  double longtitude;
  double latitude;
  double UV;
  double SoilMoisture;
  double check_sum;
};

struct NAV_POSLLH {
  unsigned char cls;
  unsigned char id;
  unsigned short len;
  unsigned long iTOW;
  long lon;
  long lat;
  long height;
  long hMSL;
  unsigned long hAcc;
  unsigned long vAcc;
};

NAV_POSLLH posllh;
String telemetry_package;


telemetry_data1 telemetryDataOnAir;
telemetry_data2 telemetryDataOnGround;

unsigned long int timeMark;
unsigned long int packetCount = 0;
int input_value;
int normalized_value;

int bmpBelowHeightCounter,gpsBelowHeightCounter;
int bmpAboveHeightCounter,gpsAboveHeightCounter;


int UVOut = A1; //analog output from the uv sensor
int hygrometer = A0; // analog output soil moisture
int REF_3V3 = A3; //3.3V power on the Funduino board
bool onGround;

SoftwareSerial GPSserial = SoftwareSerial(GPSRxPin,GPSTxPin);
SoftwareSerial XbeeSerial = SoftwareSerial(XbeeRxPin,XbeeTxPin);

Adafruit_BMP280 bmp;

void setup() {
  GPSserial.begin(38400);
  XbeeSerial.begin(9600);
  
  
  if (!bmp.begin()) {  
    XbeeSerial.println("Could not find a valid BMP280 sensor, check wiring!");
  }
  
  //uv sensor
  pinMode(UVOut, INPUT);
  pinMode(REF_3V3, INPUT);

  //motors
  pinMode(LegMotor,OUTPUT);
  pinMode(DrillMotor1,OUTPUT);
  pinMode(DrillMotor2,OUTPUT);

  digitalWrite(LegMotor,LOW); 
  digitalWrite(DrillMotor1,LOW);
  digitalWrite(DrillMotor2,LOW);

  pinMode(LegsButton,INPUT);

  bmpBelowHeightCounter = 0;
  gpsBelowHeightCounter = 0;
  bmpAboveHeightCounter=0;
  gpsAboveHeightCounter=0;
  
  if(digitalRead(LegsButton)==HIGH){
    onGround=true;
  }
  else {
    onGround = false;
  }
  
}

void loop() {

   while(!onGround){

    timeMark = millis();
    
    processGPS();

// <PACKET_COUNT>,<STATUS>,<LATITUDE>,<LONGTITUDE>,<ALTITUDE>,<PRESSURE>,<TEMPERATURE>,<CHECK_SUM> : STATUS=1 for on-flight , 2 for ground operation
    telemetryDataOnAir.latitude = (double) posllh.lat/10000000;
    telemetryDataOnAir.longtitude = (double) posllh.lon/10000000;
    telemetryDataOnAir.height = bmp.readAltitude(1013.25);//(double) posllh.height/1000.0;
    telemetryDataOnAir.pressure = bmp.readPressure();
    telemetryDataOnAir.temperature = bmp.readTemperature();

    packetCount++;
    
    telemetryDataOnAir.check_sum = packetCount
    + 1
    + telemetryDataOnAir.latitude 
    + telemetryDataOnAir.longtitude 
    + telemetryDataOnAir.height 
    + telemetryDataOnAir.pressure 
    + telemetryDataOnAir.temperature; 

    
    telemetry_package= String(packetCount) + "," 
    + String(1) + "," 
    + String(telemetryDataOnAir.latitude) + "," 
    + String(telemetryDataOnAir.longtitude) + "," 
    + String(telemetryDataOnAir.height) + "," 
    + String(telemetryDataOnAir.pressure) + "," 
    + String(telemetryDataOnAir.temperature) + "," 
    + String(telemetryDataOnAir.check_sum); 

    XbeeSerial.println(telemetry_package);
   
    if(telemetryDataOnAir.height <= BMP_HEIGHT ){
      bmpBelowHeightCounter++;
      bmpAboveHeightCounter=0;
    }
    else if (telemetryDataOnAir.height < 3000){
      bmpBelowHeightCounter = 0;
      bmpAboveHeightCounter++;
    }

    double gps_height = (double) posllh.height/1000.0;
    
    if(gps_height <= GPS_HEIGHT && gps_height!=0){
      gpsBelowHeightCounter++;
      gpsAboveHeightCounter=0;
    }
    else if(gps_height!=0) {
      gpsBelowHeightCounter = 0;
      gpsAboveHeightCounter++;
    }

    File dataFile = SD.open("datalog.txt" , FILE_WRITE );
    
    if(dataFile){
      dataFile.println(telemetry_package);
      dataFile.close();
    }

    if( didWeLaunch() ){
      EEPROM.write(0,73);
    }
    
    if(didWeLand() && EEPROM.read(0)==73){
      onGround=true;
    }
    
    delay(1000-(millis()-timeMark)); // processing power wasted

  }

  while(onGround){

    if( digitalRead(LegsButton) == LOW ){
      digitalWrite(LegMotor,HIGH);
      while(digitalRead(LegsButton)== LOW);
      digitalWrite(LegMotor,LOW);


      digitalWrite(DrillMotor1,HIGH);
      delay(30000);
      digitalWrite(DrillMotor1,LOW);
    
      digitalWrite(DrillMotor2,HIGH);
      delay(30000);
      digitalWrite(DrillMotor2,LOW);
      
    }

    while(73){
      timeMark = millis();
      processGPS();
      
      int uvlevel = averageAnalogRead(UVOut);
      int refLevel = averageAnalogRead(REF_3V3);
      float outputVoltage = 3.3 / refLevel * uvlevel;
      float uvIntensity = mapfloat(outputVoltage, 0.96, 2.9, 0.0, 15.0);

      input_value = analogRead(hygrometer);
      normalized_value = map(input_value, 0, 800, 0, 100);
      if (normalized_value > 800){
        normalized_value = 800;
      }
       
      packetCount++;

      telemetryDataOnGround.latitude = (double) posllh.lat/10000000;
      telemetryDataOnGround.longtitude = (double) posllh.lon/10000000;
      telemetryDataOnGround.UV = uvIntensity;
      telemetryDataOnGround.SoilMoisture = normalized_value;

      telemetryDataOnGround.check_sum = packetCount
      + 2
      + telemetryDataOnGround.latitude
      + telemetryDataOnGround.longtitude
      + telemetryDataOnGround.UV
      + telemetryDataOnGround.SoilMoisture;

      //<PACKET_COUNT>,2,<LATITUDE>,<LONGTITUDE>,<UV_RADIATION>,<SOIL MOISTURE>,<CHK_SUM>
      telemetry_package= String(packetCount) + "," 
      + String(2) + "," 
      + String(telemetryDataOnGround.latitude) + "," 
      + String(telemetryDataOnGround.longtitude) + "," 
      + String(telemetryDataOnGround.UV) + ","
      + String(telemetryDataOnGround.SoilMoisture) + ","
      + String(telemetryDataOnGround.check_sum); 

      XbeeSerial.println(telemetry_package);

      
      File dataFile = SD.open("datalog.txt" , FILE_WRITE );
    
      if(dataFile){
       dataFile.println(telemetry_package);
       dataFile.close();
      }
      delay(1000-(millis()-timeMark));
    }
  }

}

bool didWeLaunch(){
  return ( (bmpAboveHeightCounter>5 && gpsAboveHeightCounter>5 ) || (bmpAboveHeightCounter>10) || (gpsAboveHeightCounter>10) );
}

bool didWeLand(){
  return ( ( bmpBelowHeightCounter>=60 && gpsBelowHeightCounter>=60 ) || ( bmpBelowHeightCounter>=100 ) || ( gpsBelowHeightCounter>=100 ) );
}

//////////-Functions for UV-//////////
int averageAnalogRead(int pinToRead)
{
  byte numberOfReadings = 8;
  unsigned int runningValue = 0; 

  for(int x = 0 ; x < numberOfReadings ; x++)
    runningValue += analogRead(pinToRead);
  runningValue /= numberOfReadings;

  return(runningValue);  
}

float mapfloat(float x, float in_min, float in_max, float out_min, float out_max)
{
  return (x - in_min) * (out_max - out_min) / (in_max - in_min) + out_min;
}
//////////

//////////- Functions for GPS data parsing-//////////
const unsigned char UBX_HEADER[] = { 0xB5, 0x62 };

void calcChecksum(unsigned char* CK) {
  memset(CK, 0, 2);
  for (int i = 0; i < (int)sizeof(NAV_POSLLH); i++) {
    CK[0] += ((unsigned char*)(&posllh))[i];
    CK[1] += CK[0];
  }
}

bool processGPS() {
  static int fpos = 0;
  static unsigned char checksum[2];
  const int payloadSize = sizeof(NAV_POSLLH);

  while ( GPSserial.available() ) {
    byte c = GPSserial.read();
    if ( fpos < 2 ) {
      if ( c == UBX_HEADER[fpos] )
        fpos++;
      else
        fpos = 0;
    }
    else {
      if ( (fpos-2) < payloadSize )
        ((unsigned char*)(&posllh))[fpos-2] = c;

      fpos++;

      if ( fpos == (payloadSize+2) ) {
        calcChecksum(checksum);
      }
      else if ( fpos == (payloadSize+3) ) {
        if ( c != checksum[0] )
          fpos = 0;
      }
      else if ( fpos == (payloadSize+4) ) {
        fpos = 0;
        if ( c == checksum[1] ) {
          return true;
        }
      }
      else if ( fpos > (payloadSize+4) ) {
        fpos = 0;
      }
    }
  }
  return false;
}
//////////

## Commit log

2018-04-13 Added Arduino's code and configuration files from xbee and gps
2018-04-13 Added the circuit designs by Dimitris Bralios
    [Adafruit MCP73871 Solar Charger v4.brd, Adafruit MCP73871 Solar Charger v4.sch, Li_Power_Boost_Converter.brd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]

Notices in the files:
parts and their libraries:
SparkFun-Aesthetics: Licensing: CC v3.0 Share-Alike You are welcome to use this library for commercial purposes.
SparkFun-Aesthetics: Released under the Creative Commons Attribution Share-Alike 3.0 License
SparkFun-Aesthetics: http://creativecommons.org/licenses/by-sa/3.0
